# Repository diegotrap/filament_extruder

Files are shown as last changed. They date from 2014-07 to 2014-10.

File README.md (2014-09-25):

Filament Extruder
=================

Filament Extruder is a project dedicated to develop a simple, economic and easy to build filament extruding machine. It starts as an academic project at University Carlos III of Madrid.

Currently, the project is being prototyped and documented. The features of the present prototype are:

* Variable speed drive.
* Three independent temperature zones.
* Modular design, subsystems are mounted on an aluminium rail.
* Arduino controlled.
* LCD and encoder user interface.
* Variable speed pulling system.
* Fan cooling system.

Extruded product results have been documented to be:

* Filament usable for 3D printing.
* Up to 0.4 kg/h throughput.
* Up to +- 0.49 mm tolerance (quite bad result by now).

A video of the machine working can be found at http://youtu.be/RHb1_fSeXK4.

Images of the extrusion system:

*Extrusion line:*

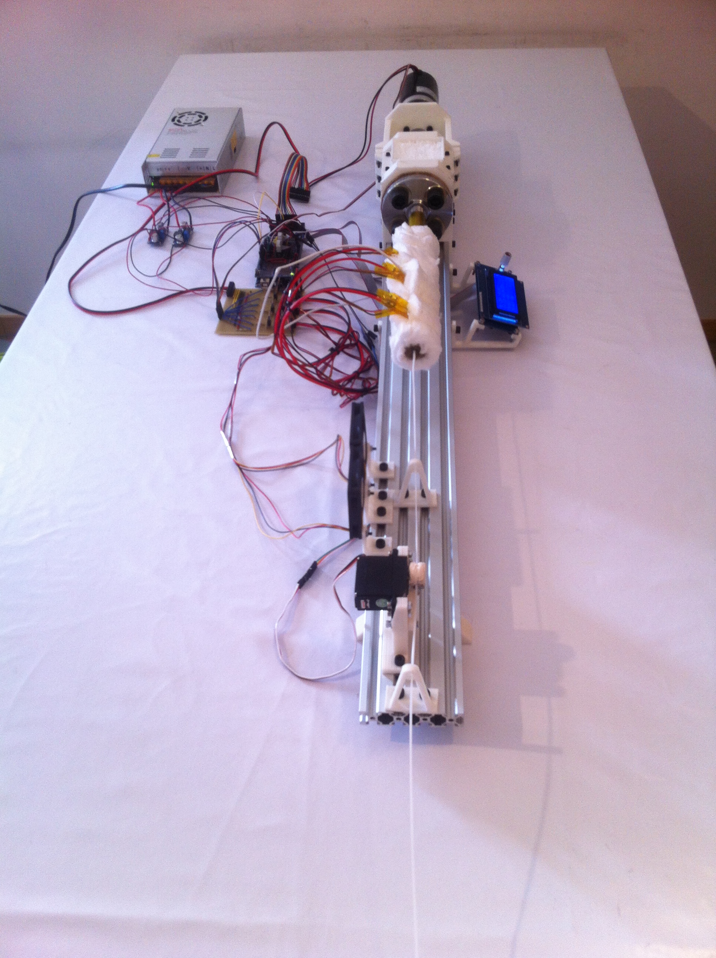
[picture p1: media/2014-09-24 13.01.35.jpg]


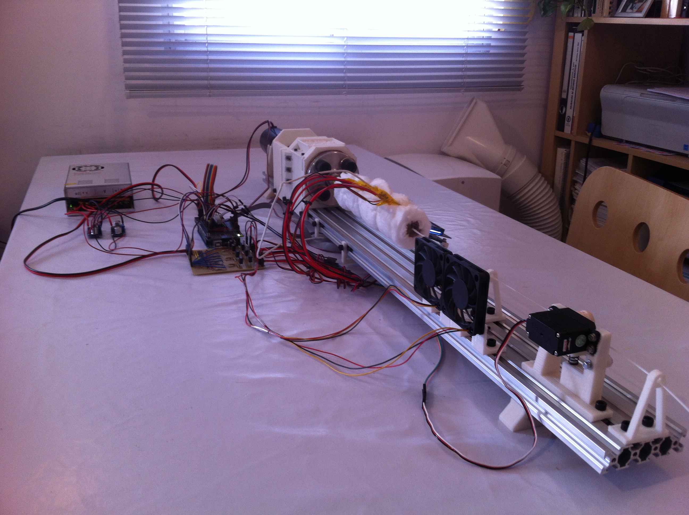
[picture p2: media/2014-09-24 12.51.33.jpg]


*Puller and cooling fans:*

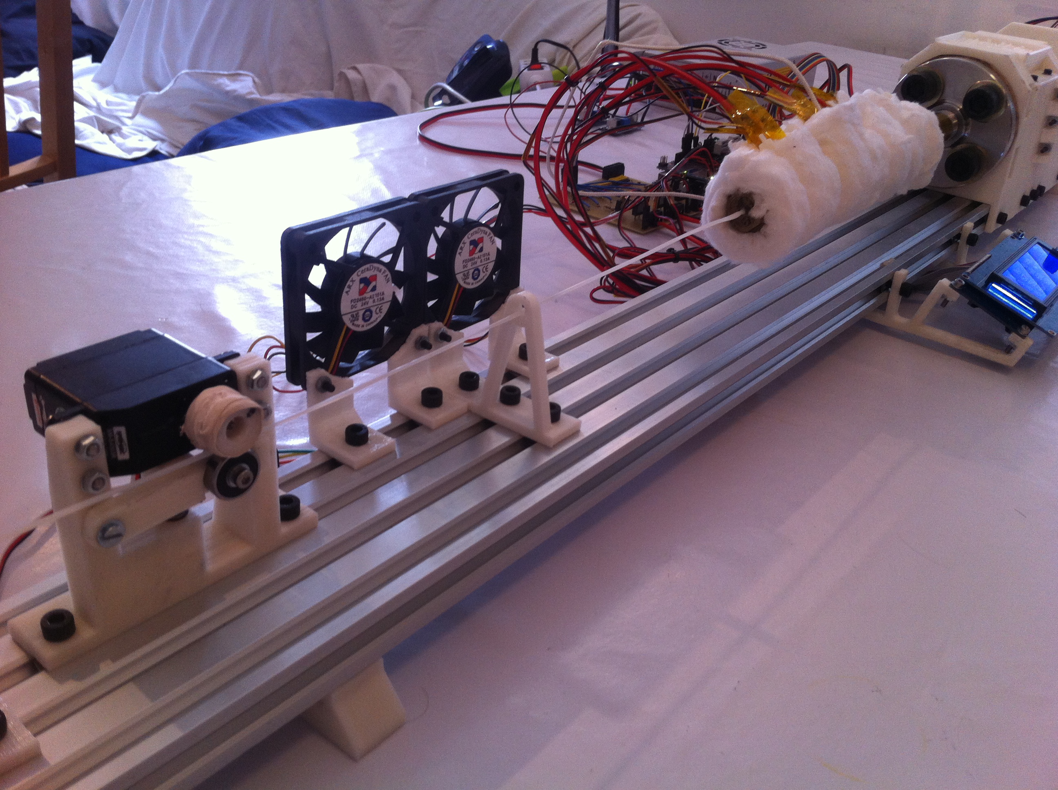
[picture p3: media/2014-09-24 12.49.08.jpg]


*Extruder and electronics:*

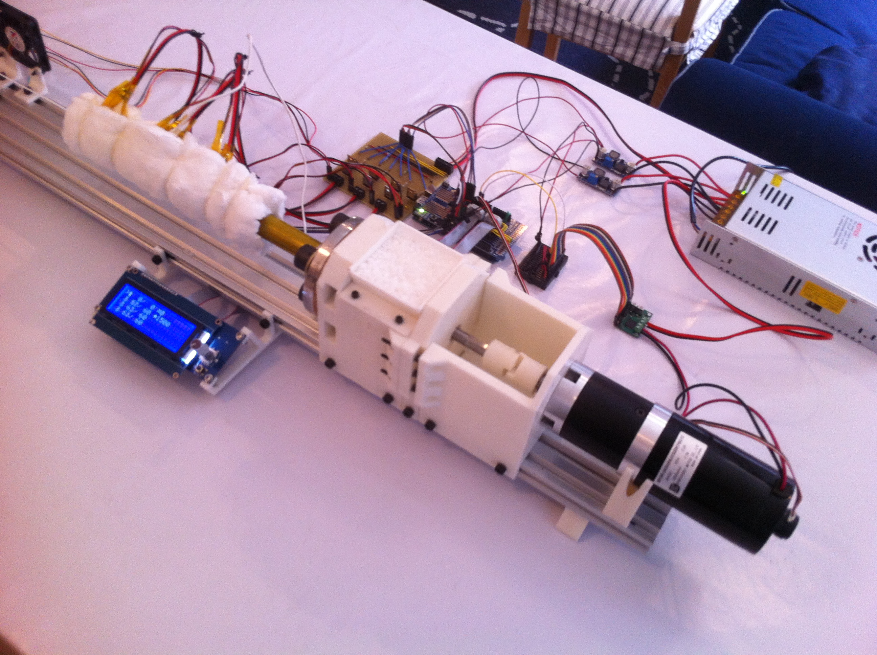
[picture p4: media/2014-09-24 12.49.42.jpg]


*Extruder body:*

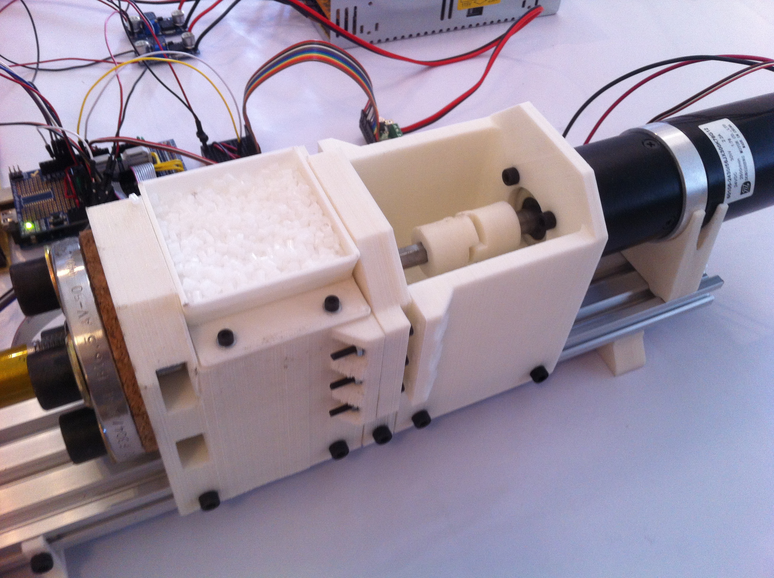
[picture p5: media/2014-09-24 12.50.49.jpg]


*Electronics:*

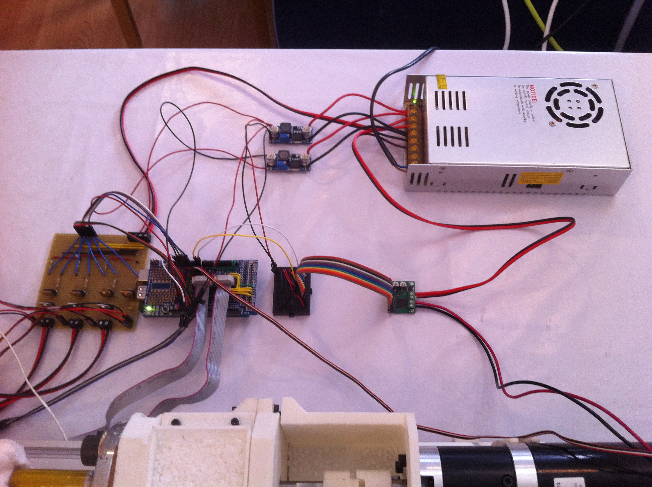
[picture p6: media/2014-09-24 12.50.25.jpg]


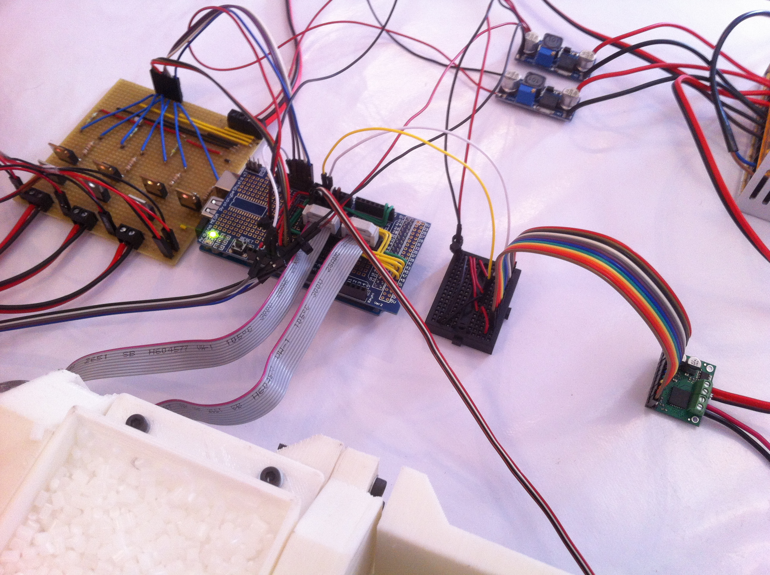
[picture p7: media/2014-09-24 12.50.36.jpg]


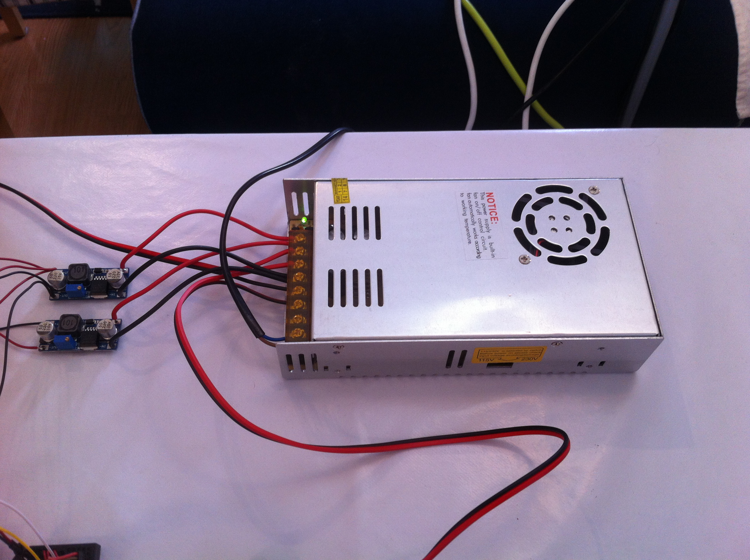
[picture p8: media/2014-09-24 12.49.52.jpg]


*LCD+encoder interface:*

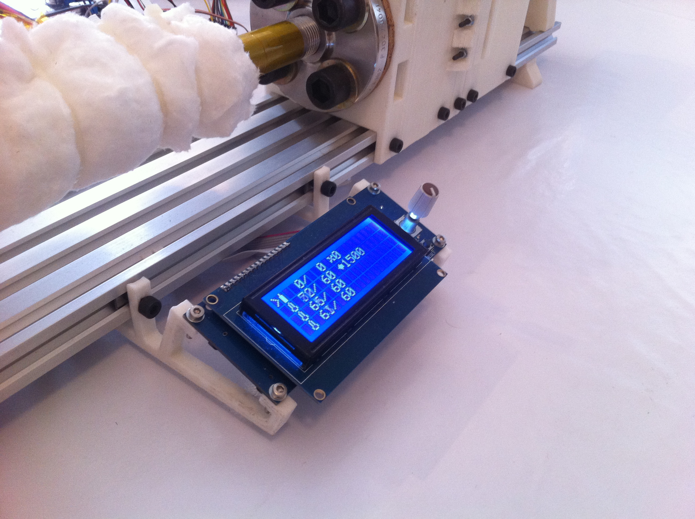
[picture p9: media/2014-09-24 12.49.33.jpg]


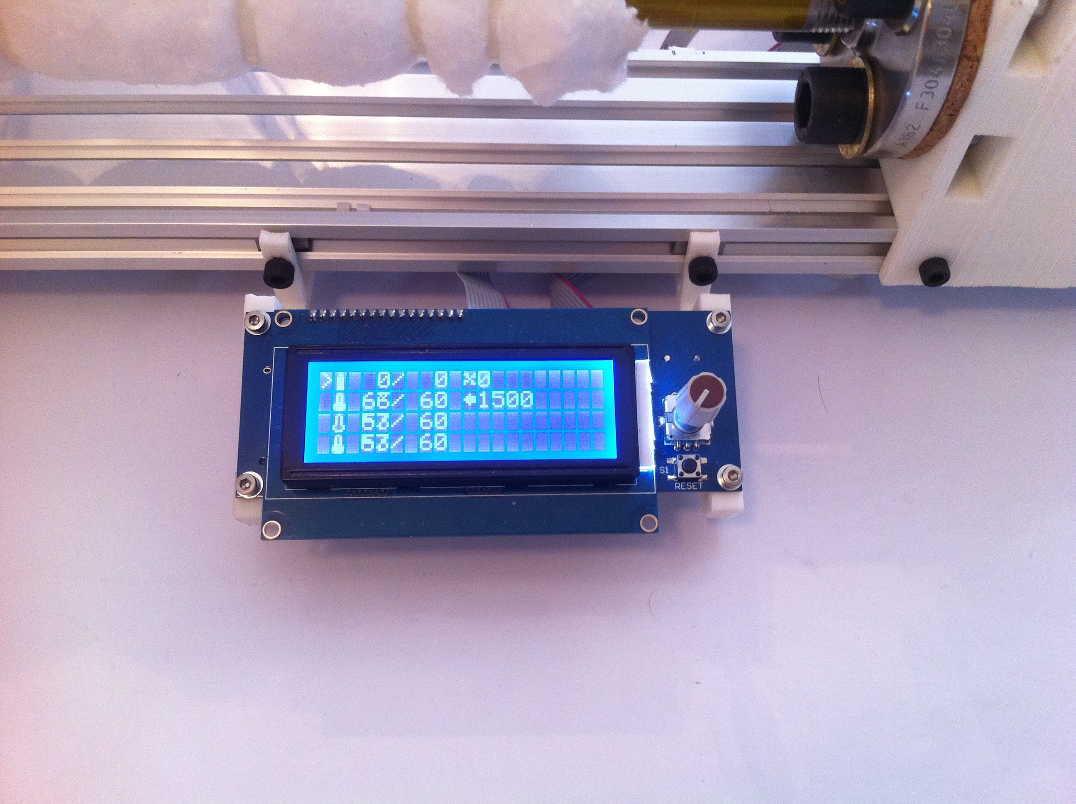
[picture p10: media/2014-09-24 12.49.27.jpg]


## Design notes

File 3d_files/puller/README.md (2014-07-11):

# Puller

**Note:** This is a first prototype of the puller and a work in progress. 

The **puller** is a subsystem of the filament extruder line that hauls off the solidified filament coming out of the extruder at a controlled speed.

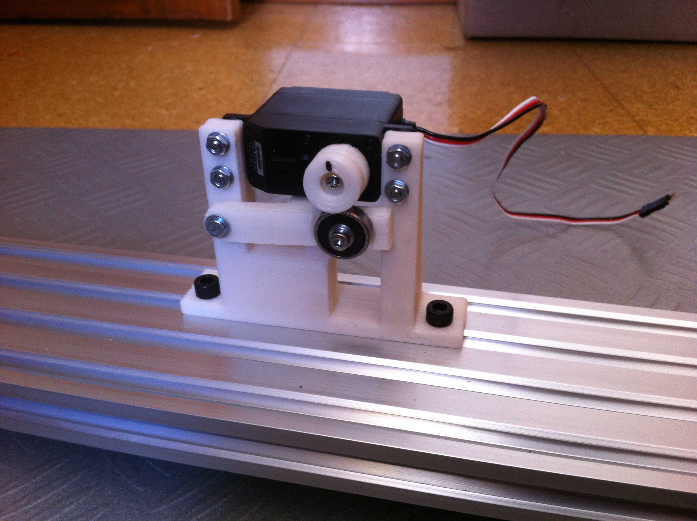
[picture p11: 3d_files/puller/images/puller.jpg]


## Parts

The parts necessary for building one puller (first prototype) are:

* 1 `puller_structure_simplified_fixed` (printed part)
* 1 `puller_lever_with_spring` (printed part)
* 1 `puller_wheel` (printed part)
* 1 continuous rotation servo (I use this one: http://www.pololu.com/product/1248)
* 1 625-2RS radial ball bearing
* 1 spring
* 5 M3x16 screws
* 1 M3x20 screw
* 5 M3 nuts
* 1 M3 self-locking nut
* 13 M3 washers
* Optional: 2 M5x10 screws and 2 t-nuts are necessary for fixing the puller to a v-slot profile.

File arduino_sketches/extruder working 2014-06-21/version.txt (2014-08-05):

versión que tiene el menú de pantalla y algunas funciones como RGB Led, etc, pero presenta bugs en la interfaz

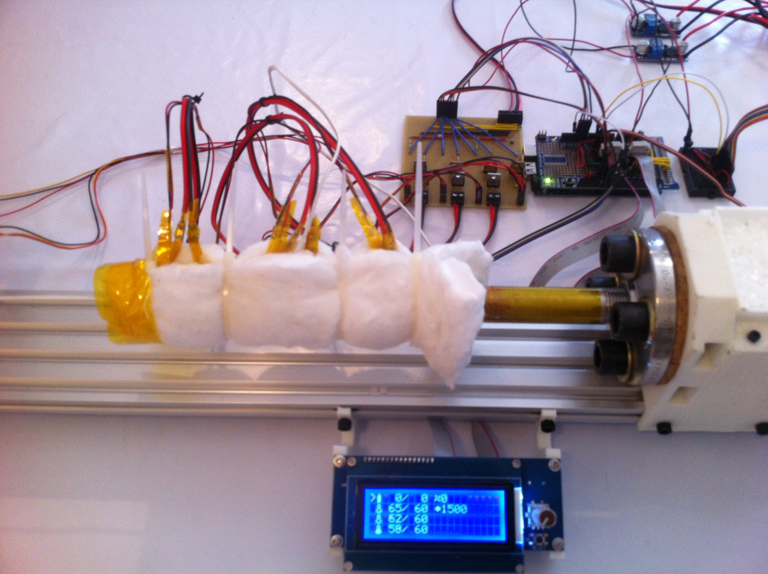
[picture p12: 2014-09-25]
media/2014-09-24 12.47.06.jpg

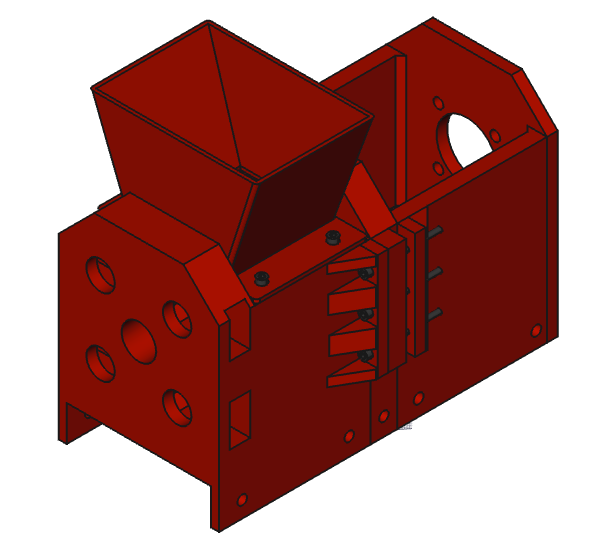
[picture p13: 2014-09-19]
media/FreeCAD_4.png

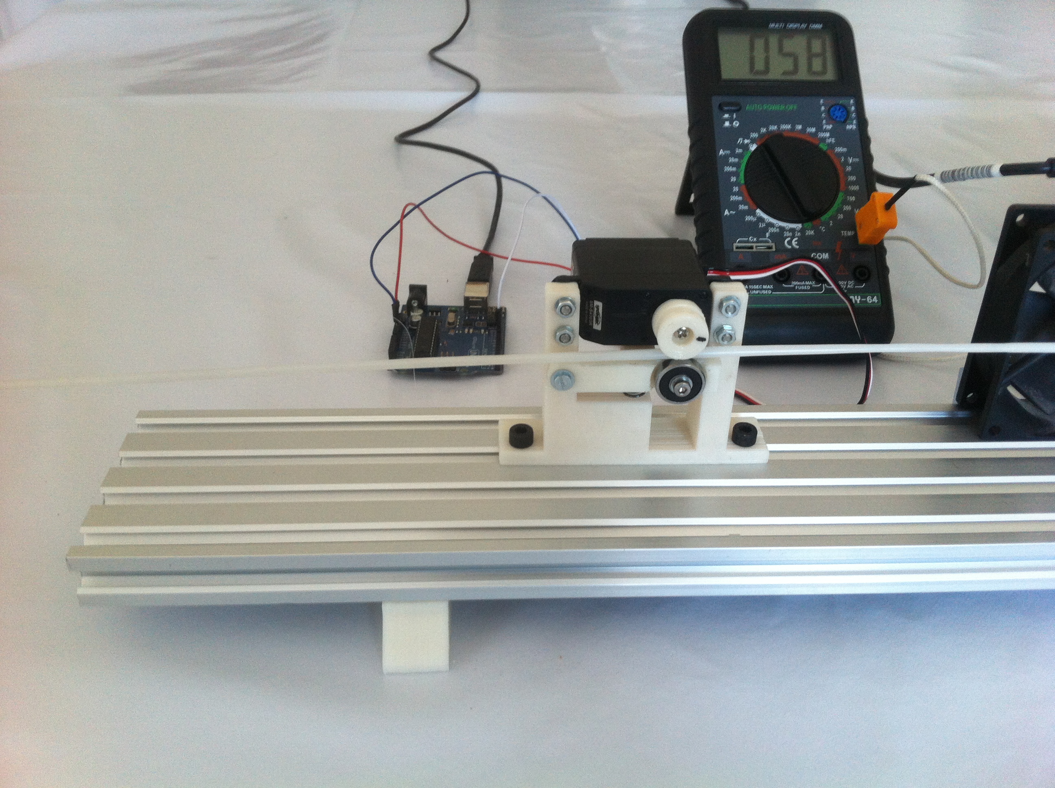
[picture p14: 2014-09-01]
media/2014-08-16 19.02.47.jpg

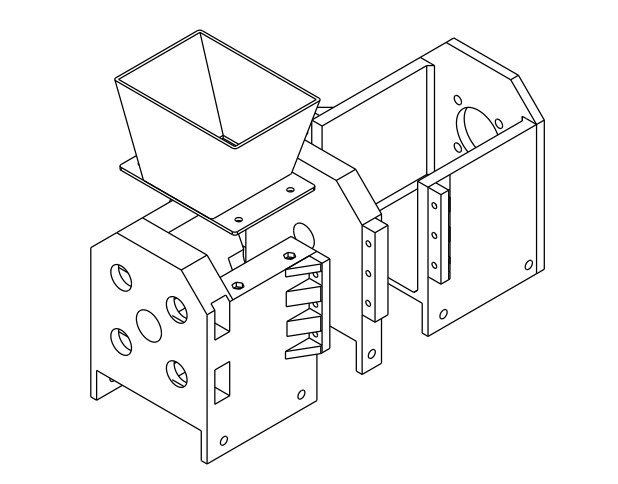
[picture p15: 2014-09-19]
media/unibody_drive_exploded_view_pdf__1_page_.png

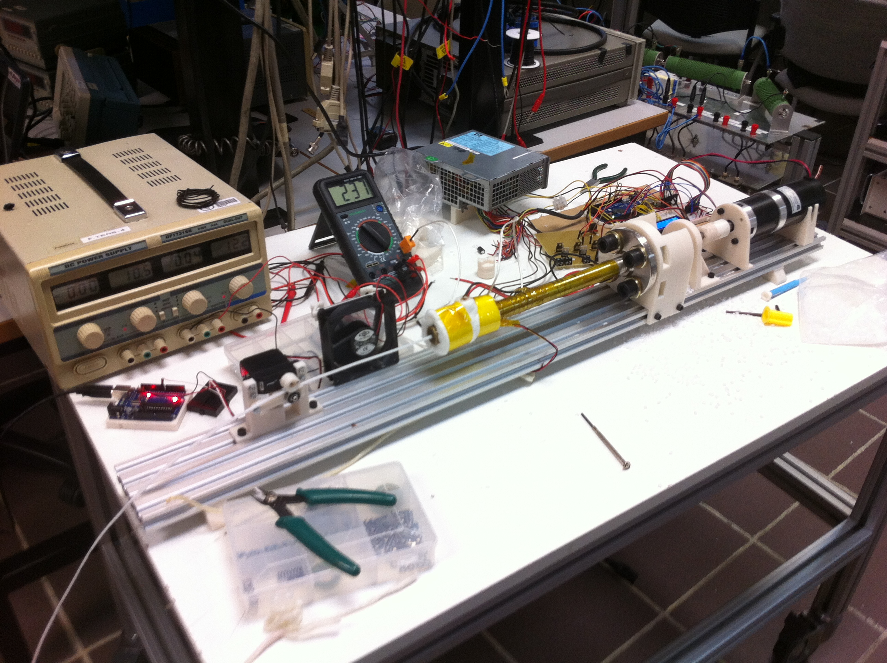
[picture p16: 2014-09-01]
media/2014-07-29 19.45.26.jpg

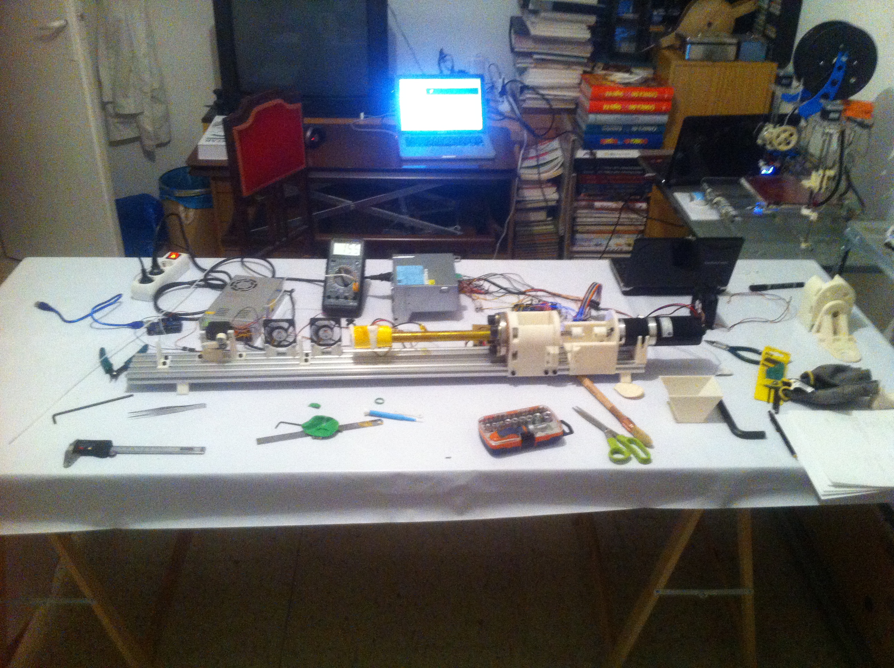
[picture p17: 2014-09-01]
media/2014-08-18 22.53.50.jpg

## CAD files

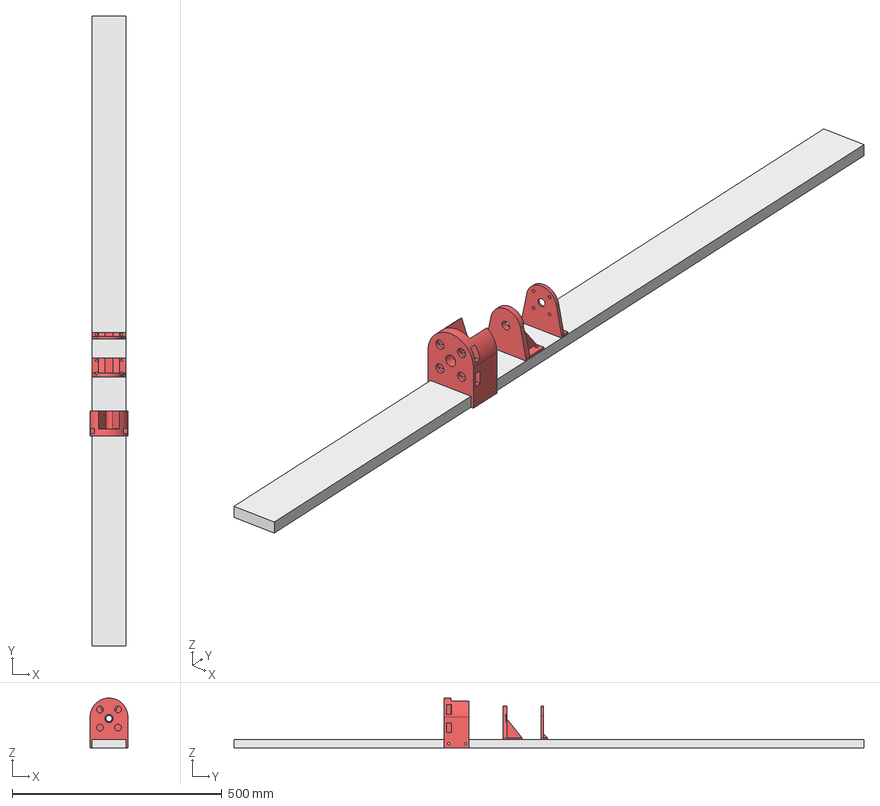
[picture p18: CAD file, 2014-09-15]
3d_files/drive/first_prototype/prototype_assembly.fcstd
90.0 x 1500.0 x 118.8 mm
hopper_and_barrel_support
thrust_bearing_support
motor_support
vslot

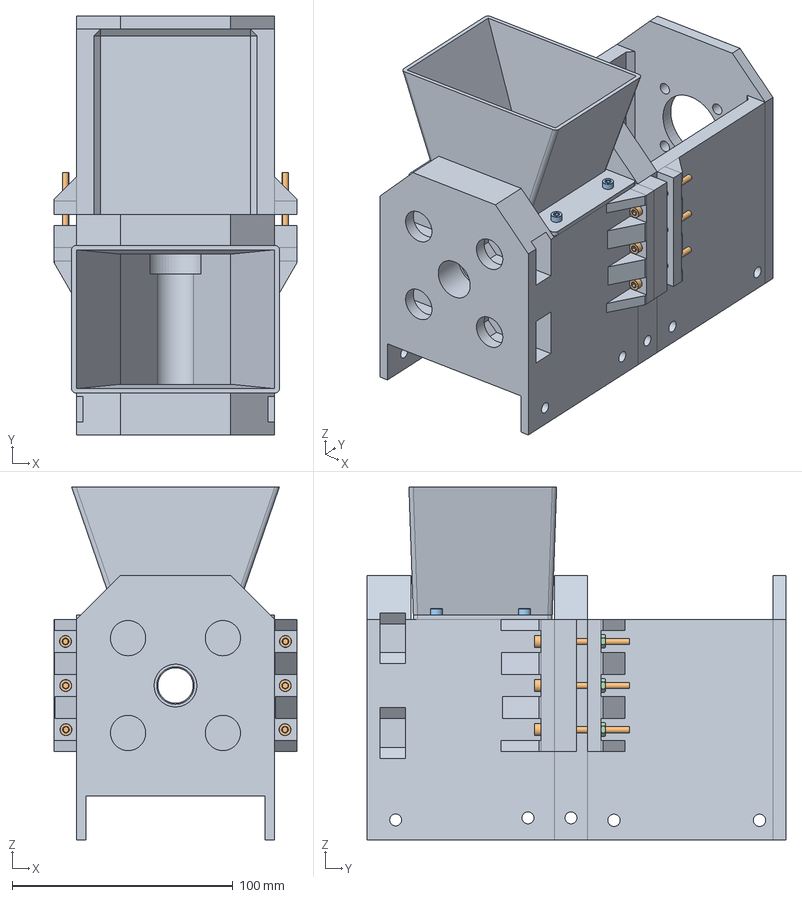
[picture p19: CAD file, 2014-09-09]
3d_files/drive/unibody_drive_i2/assembly/unibody_drive_assembled.fcstd
110.0 x 190.0 x 160.0 mm
printed_parts
M3x40_screws
M3_hopper_screws
M3_nuts

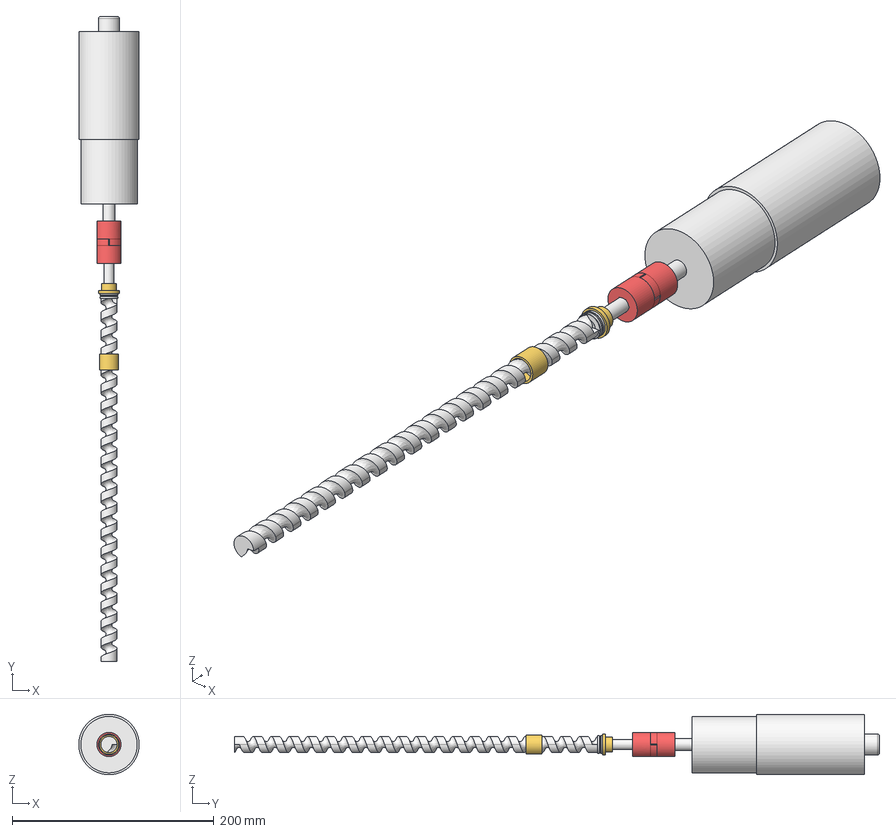
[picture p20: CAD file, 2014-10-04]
3d_files/extruder_assembly/mechanical_assembly.fcstd
59.9 x 640.0 x 60.0 mm
flanged_bearing
plain_bearing
thrust_bearing
motor
shaft_coupler_hex
shaft_coupler_keyway
screw

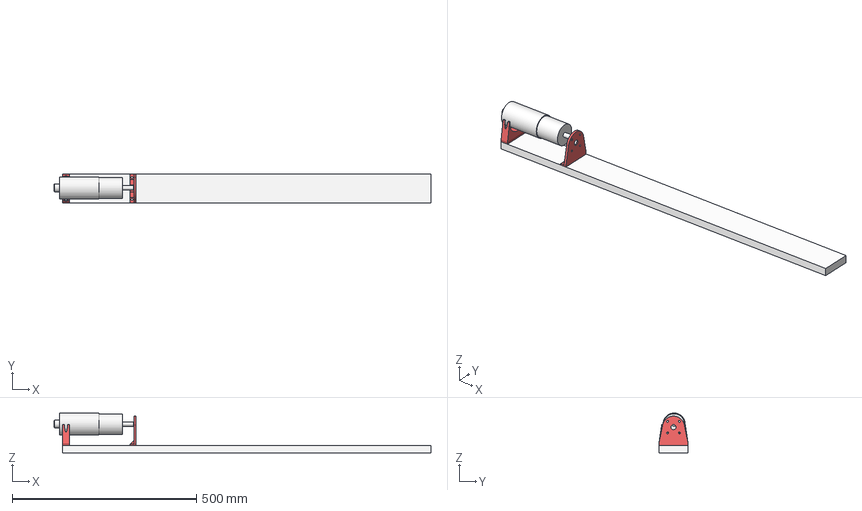
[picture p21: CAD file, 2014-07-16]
3d_files/filament_line_assembly.fcstd
1022.5 x 80.0 x 108.4 mm
vslot
motor_torsion_support
vslot_motor_support_big
motor_simplified

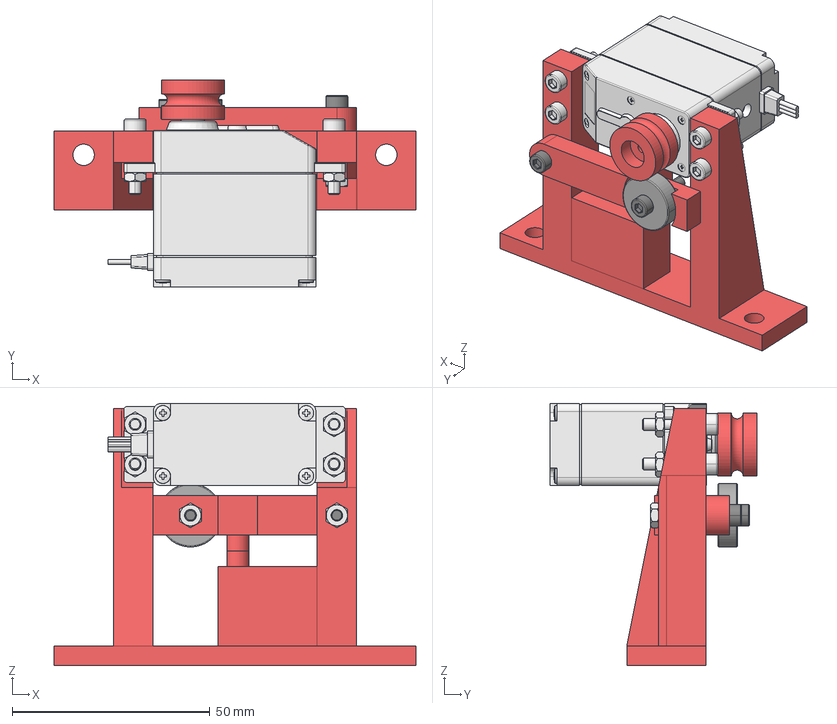
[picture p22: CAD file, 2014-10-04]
3d_files/extruder_assembly/puller_assembly.fcstd
91.5 x 52.3 x 66.3 mm
puller_structure
puller_lever
M3x20_001
625-2RS_ball_bearing
M3x16_001
M3_nut_001
M3_nut_002
Servo-SM-S4303R
servo_nuts_and_bolts
puller_wheel

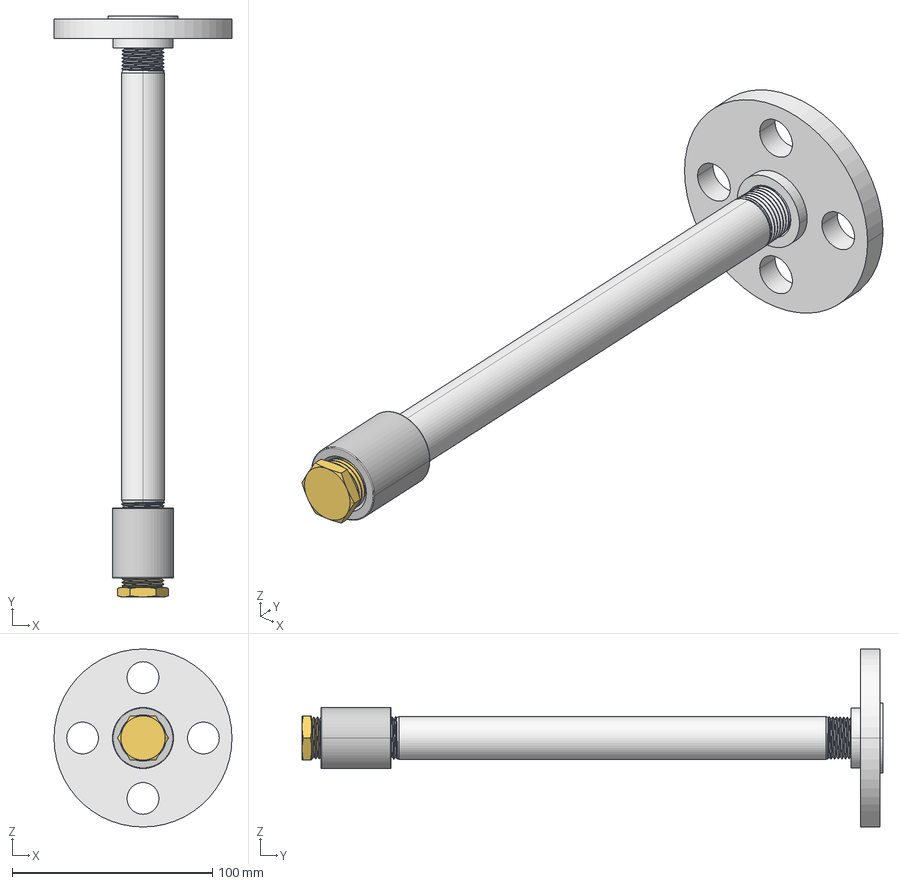
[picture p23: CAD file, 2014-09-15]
3d_files/barrel/barrel_assembly.fcstd
88.9 x 290.1 x 88.9 mm
4452K114
4452K144
4548K181
44695K11

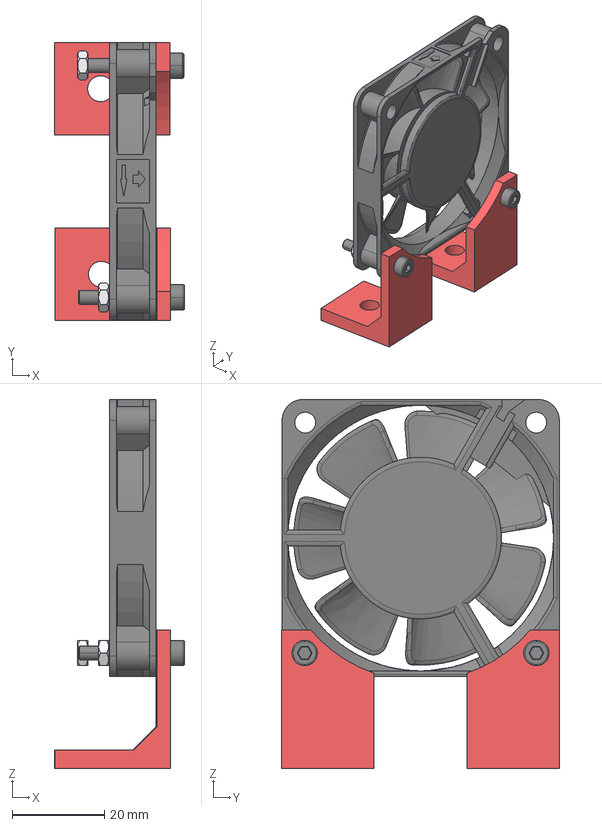
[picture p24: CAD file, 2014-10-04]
3d_files/extruder_assembly/fan_assembly.fcstd
28.2 x 60.1 x 79.9 mm
DC_fan_60x60x10
fan_holder_right
M3x20_004
M3x20_003
M3_nut_007
M3_nut_008
fan_holder_left

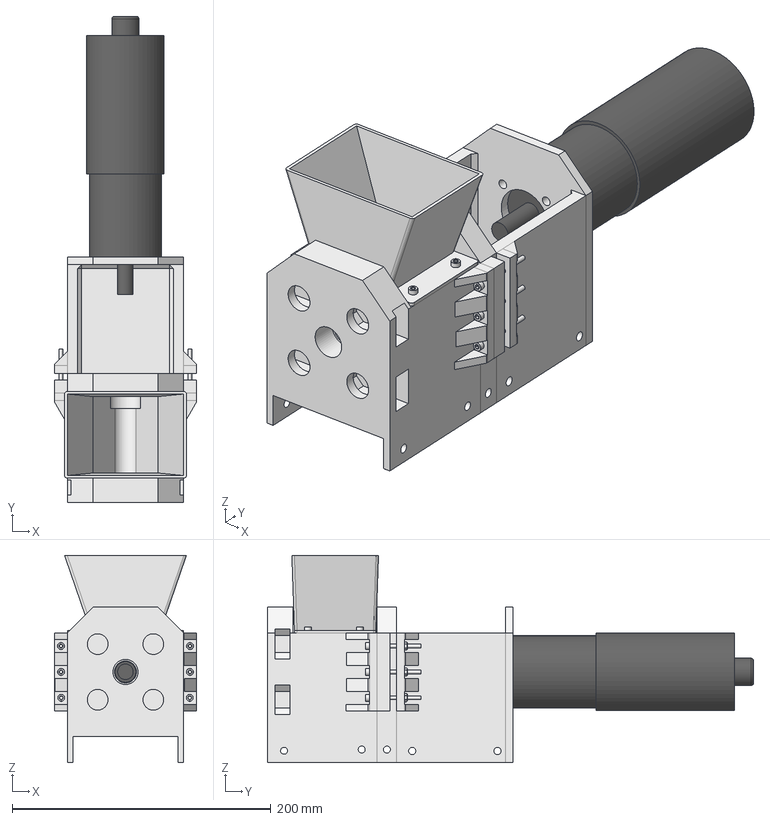
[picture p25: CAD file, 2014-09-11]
3d_files/extruder_assembly/unibody_drive_assembled.fcstd
110.0 x 376.0 x 160.0 mm
printed_parts
M3x40_screws
M3_hopper_screws
M3_nuts
motor

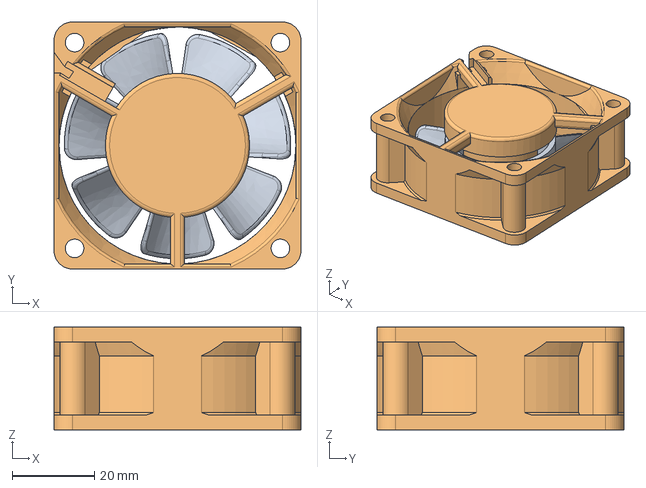
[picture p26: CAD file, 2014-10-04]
3d_files/cooling/Fan 60x60x25mm.stp
60.0 x 60.0 x 25.0 mm

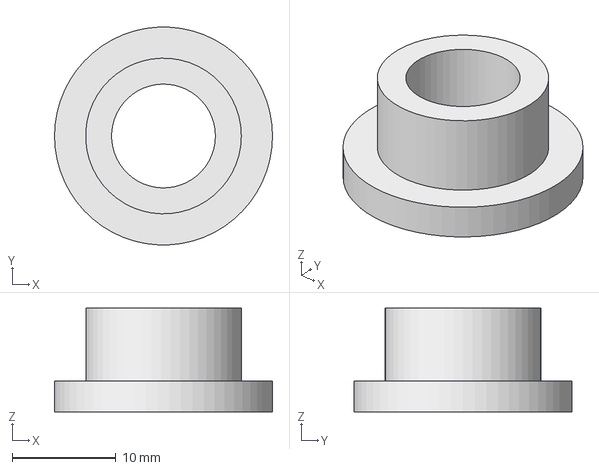
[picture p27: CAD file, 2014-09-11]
3d_files/drive/bearings/flanged_bearing.fcstd
21.0 x 21.0 x 10.0 mm

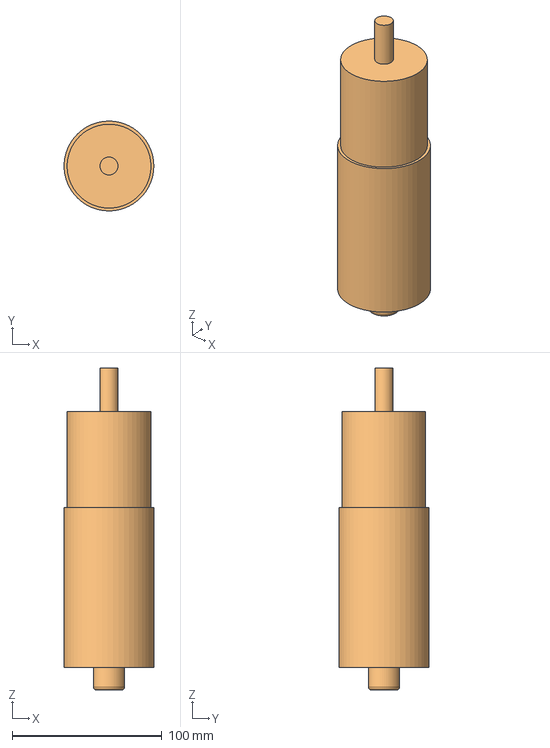
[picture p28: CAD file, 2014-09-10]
3d_files/drive/motor/motor_simplified.fcstd
59.9 x 60.0 x 215.0 mm

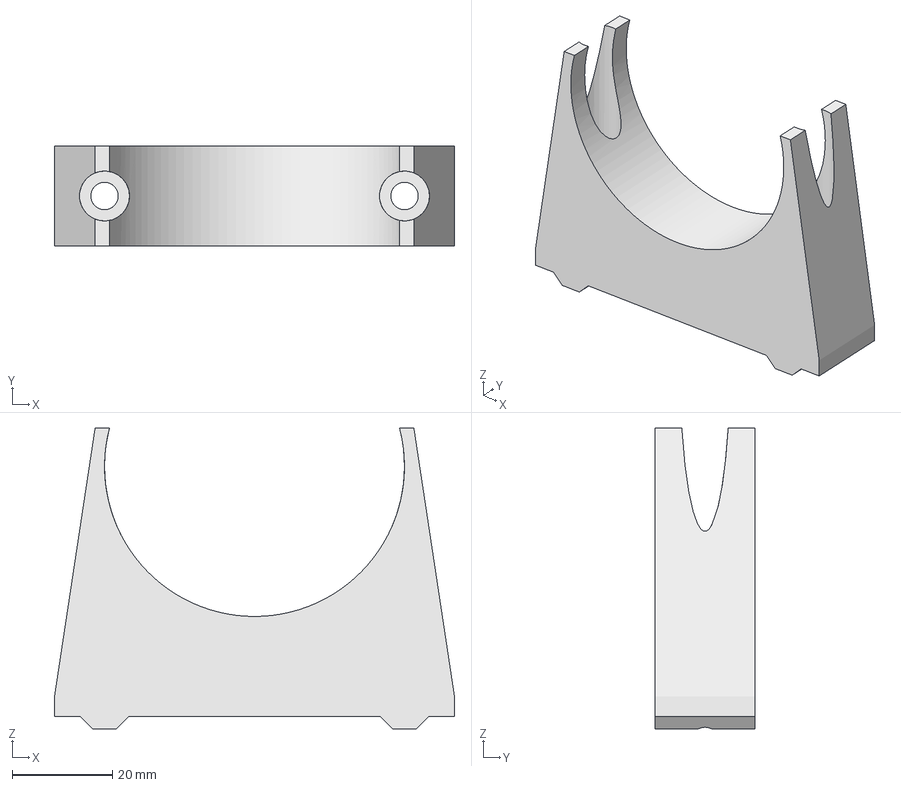
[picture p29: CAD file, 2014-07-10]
3d_files/drive/motor_weight_supports/vslot_motor_support_big.fcstd
80.0 x 20.0 x 60.2 mm

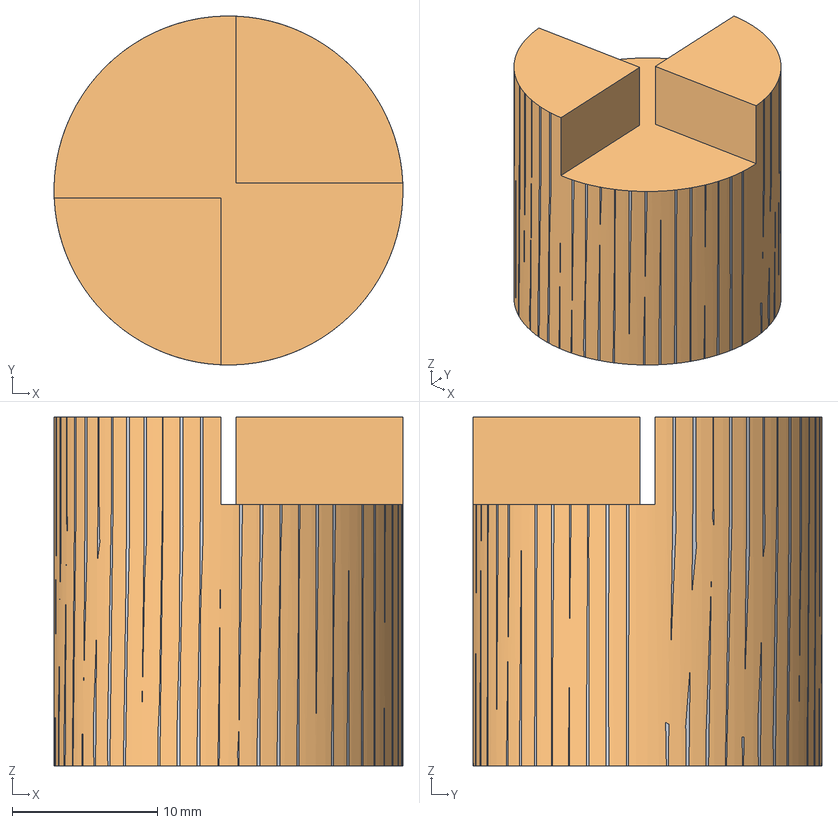
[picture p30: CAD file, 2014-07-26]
3d_files/drive/shaft_couplers/shaft_coupler_hex.fcstd
24.0 x 24.0 x 24.0 mm
Pocket (Meshed)

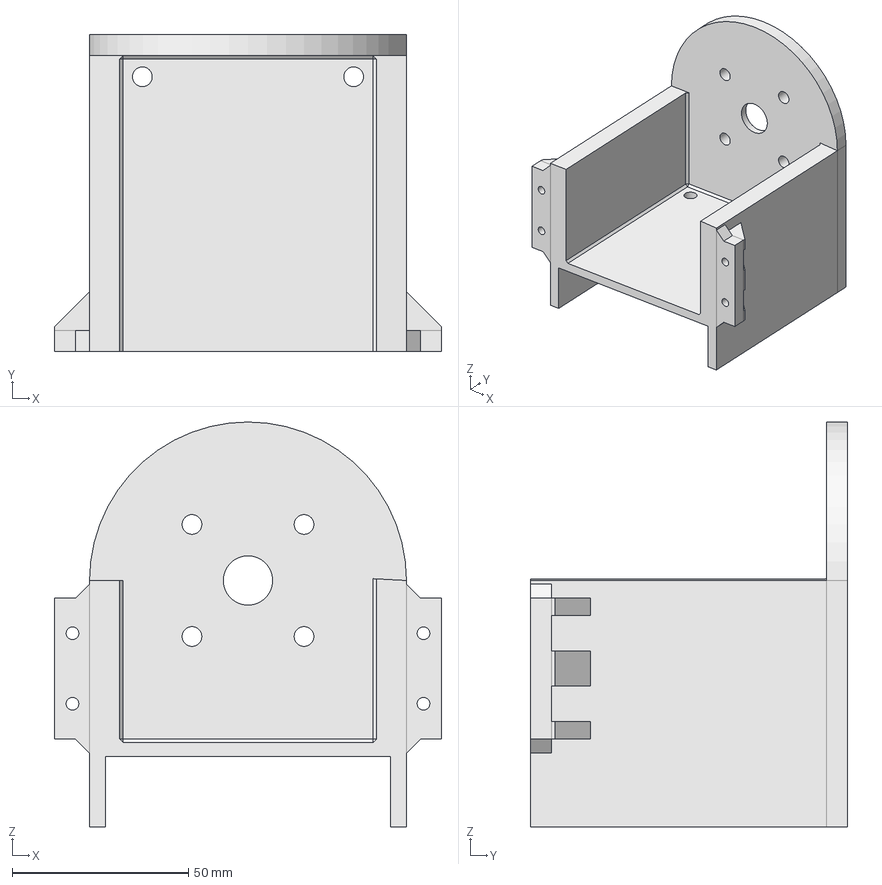
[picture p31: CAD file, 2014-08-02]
3d_files/drive/unibody_drive/motor_support.fcstd
110.0 x 90.0 x 115.0 mm

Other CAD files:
3d_files/drive/unibody_drive_i2/parts/thrust_bearing_support.fcstd
3d_files/other/lcd_holder.fcstd
3d_files/puller/bearing_625_0.stp
3d_files/spool/spool.FCStd
3d_files/barrel/4452K114.STEP
3d_files/barrel/4452K144.STEP
3d_files/barrel/44695K110.STEP
3d_files/barrel/4548K181.STEP
3d_files/cooling/DC_fan_60x60x10.FCStd
3d_files/cooling/fan_duct.fcstd
3d_files/cooling/fan_holder_left.fcstd
3d_files/cooling/fan_holder_left.stl
3d_files/cooling/fan_holder_right.fcstd
3d_files/cooling/fan_holder_right.stl
3d_files/cooling/fan_support.fcstd
3d_files/cooling/vslot_fan_foot.fcstd
3d_files/drive/bearings/plain_bearing.FCStd
3d_files/drive/bearings/thrust_bearing.fcstd
3d_files/drive/first_prototype/motor_torsion_support.fcstd
3d_files/drive/first_prototype/motor_torsion_support.stl
3d_files/drive/first_prototype/pipe_and_hopper_strong.fcstd
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

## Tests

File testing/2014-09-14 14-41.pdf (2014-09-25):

## Datos de la muestra

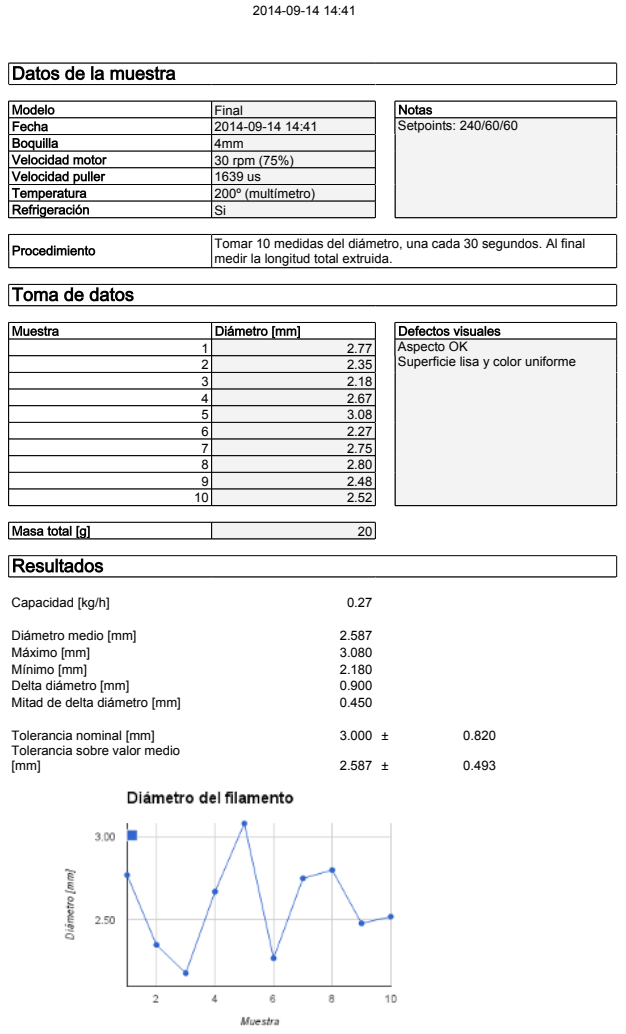
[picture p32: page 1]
Modelo; Final; Notas; Fecha; Setpoints: 240/60/60; Procedimiento; Tomar 10 medidas del diámetro, una cada 30 segundos. Al final; Muestra; Diámetro [mm]; Defectos visuales; Aspecto OK; Superficie lisa y color uniforme; Masa total [g]; Resultados; Capacidad [kg/h]; Diámetro medio [mm]; Máximo [mm]; Mínimo [mm]; Delta diámetro [mm]; Mitad de delta diámetro [mm]; Tolerancia nominal [mm]

Boquilla | 4mm
Velocidad motor | 30 rpm (75%)
Velocidad puller | 1639 us
Temperatura | 200º (multímetro)
Refrigeración | Si

medir la longitud total extruida.

Toma de datos

3 | 2.18
4 | 2.67
5 | 3.08
6 | 2.27
7 | 2.75
8 | 2.80
9 | 2.48
10 | 2.52

Tolerancia sobre valor medio

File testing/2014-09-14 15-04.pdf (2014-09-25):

## Datos de la muestra

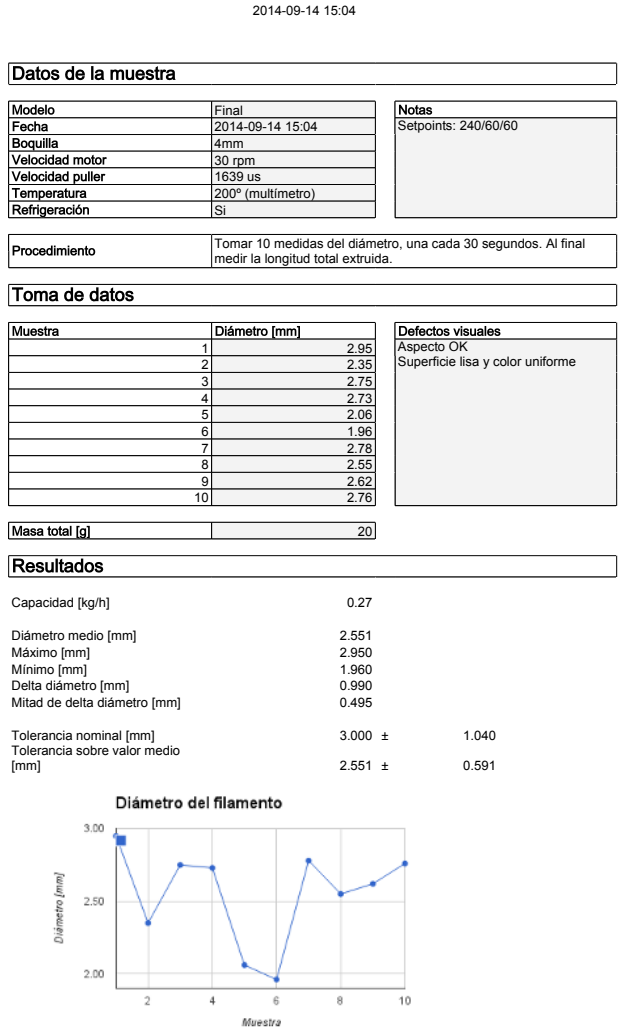
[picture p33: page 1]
Modelo; Final; Notas; Fecha; Setpoints: 240/60/60; Procedimiento; Tomar 10 medidas del diámetro, una cada 30 segundos. Al final; Muestra; Diámetro [mm]; Defectos visuales; Aspecto OK; Superficie lisa y color uniforme; Masa total [g]; Resultados; Capacidad [kg/h]; Diámetro medio [mm]; Máximo [mm]; Mínimo [mm]; Delta diámetro [mm]; Mitad de delta diámetro [mm]; Tolerancia nominal [mm]

Boquilla | 4mm
Velocidad motor | 30 rpm
Velocidad puller | 1639 us
Temperatura | 200º (multímetro)
Refrigeración | Si

medir la longitud total extruida.

Toma de datos

3 | 2.75
4 | 2.73
5 | 2.06
6 | 1.96
7 | 2.78
8 | 2.55
9 | 2.62
10 | 2.76

Tolerancia sobre valor medio

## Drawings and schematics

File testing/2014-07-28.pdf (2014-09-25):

## Datos de la muestra

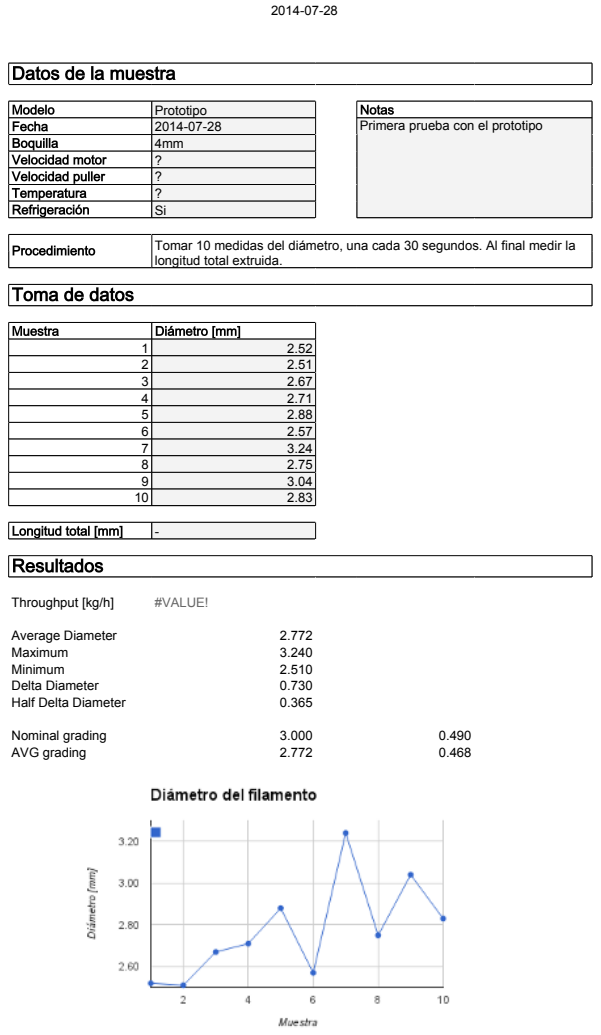
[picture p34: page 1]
Modelo; Prototipo; Notas; Fecha; Primera prueba con el prototipo; Procedimiento; Tomar 10 medidas del diámetro, una cada 30 segundos. Al final medir la; Longitud total [mm]; Resultados; Throughput [kg/h]; #VALUE!; Average Diameter; Maximum; Minimum; Delta Diameter; Half Delta Diameter; Nominal grading; AVG grading

Boquilla | 4mm
Velocidad motor | ?
Velocidad puller | ?
Temperatura | ?
Refrigeración | Si

longitud total extruida.

Toma de datos

Muestra | Diámetro [mm]

1 | 2.52
2 | 2.51
3 | 2.67
4 | 2.71
5 | 2.88
6 | 2.57
7 | 3.24
8 | 2.75
9 | 3.04
10 | 2.83

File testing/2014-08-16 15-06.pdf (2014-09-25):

## Datos de la muestra

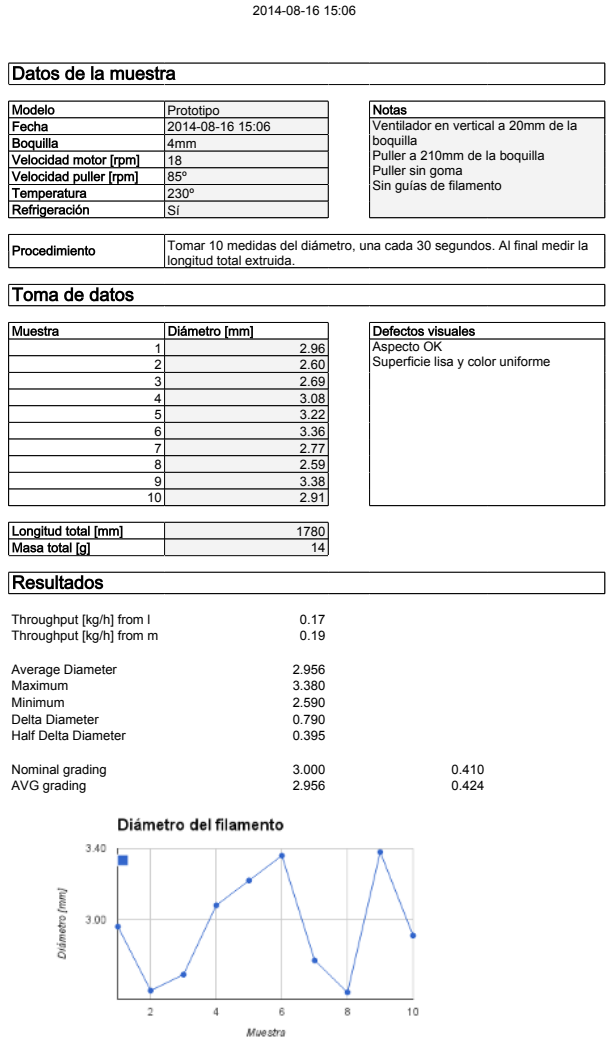
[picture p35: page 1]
Modelo; Prototipo; Notas; Fecha; Ventilador en vertical a 20mm de la; Procedimiento; Tomar 10 medidas del diámetro, una cada 30 segundos. Al final medir la; Muestra; Diámetro [mm]; Defectos visuales; Aspecto OK; Superficie lisa y color uniforme; Resultados; Throughput [kg/h] from l; Throughput [kg/h] from m; Average Diameter; Maximum; Minimum; Delta Diameter; Half Delta Diameter; Nominal grading; AVG grading

Boquilla | 4mm
Velocidad motor [rpm] | 18
Velocidad puller [rpm] | 85º
Temperatura | 230º
Refrigeración | Sí

boquilla
Puller a 210mm de la boquilla
Puller sin goma
Sin guías de filamento

longitud total extruida.

Toma de datos

3 | 2.69
4 | 3.08
5 | 3.22
6 | 3.36
7 | 2.77
8 | 2.59
9 | 3.38
10 | 2.91

Longitud total [mm] | 1780
Masa total [g] | 14

2014-08-16 15:06

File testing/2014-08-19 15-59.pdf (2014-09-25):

## Datos de la muestra

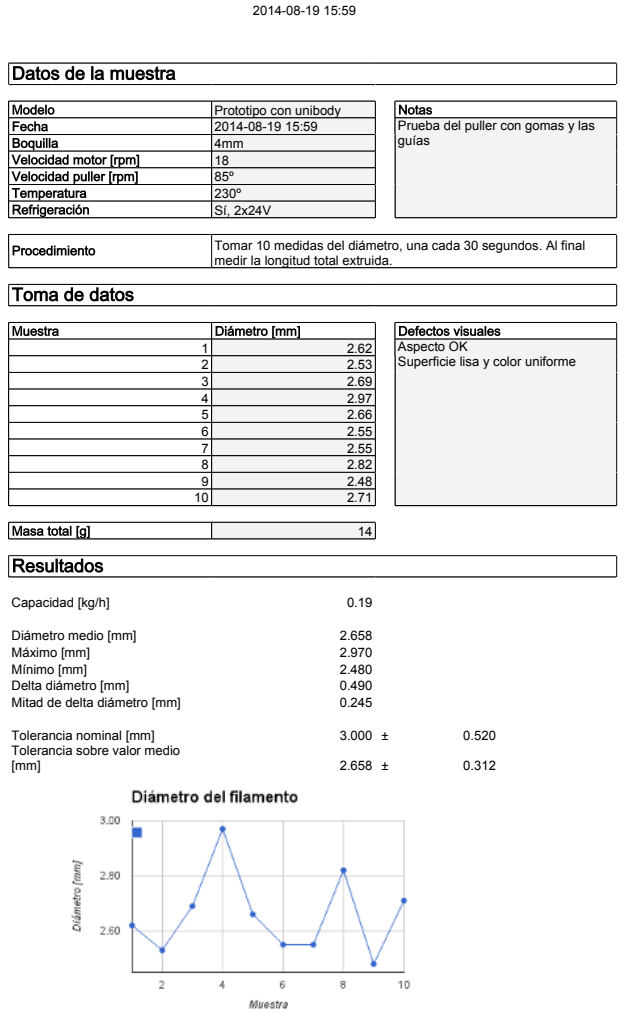
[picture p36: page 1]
Modelo; Prototipo con unibody; Notas; Fecha; Prueba del puller con gomas y las; Boquilla; guías; Procedimiento; Tomar 10 medidas del diámetro, una cada 30 segundos. Al final; Muestra; Diámetro [mm]; Defectos visuales; Aspecto OK; Superficie lisa y color uniforme; Masa total [g]; Resultados; Capacidad [kg/h]; Diámetro medio [mm]; Máximo [mm]; Mínimo [mm]; Delta diámetro [mm]; Mitad de delta diámetro [mm]; Tolerancia nominal [mm]

Velocidad motor [rpm] | 18
Velocidad puller [rpm] | 85º
Temperatura | 230º
Refrigeración | Sí, 2x24V

medir la longitud total extruida.

Toma de datos

3 | 2.69
4 | 2.97
5 | 2.66
6 | 2.55
7 | 2.55
8 | 2.82
9 | 2.48
10 | 2.71

Tolerancia sobre valor medio

2014-08-19 15:59

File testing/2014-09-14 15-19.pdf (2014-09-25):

## Datos de la muestra

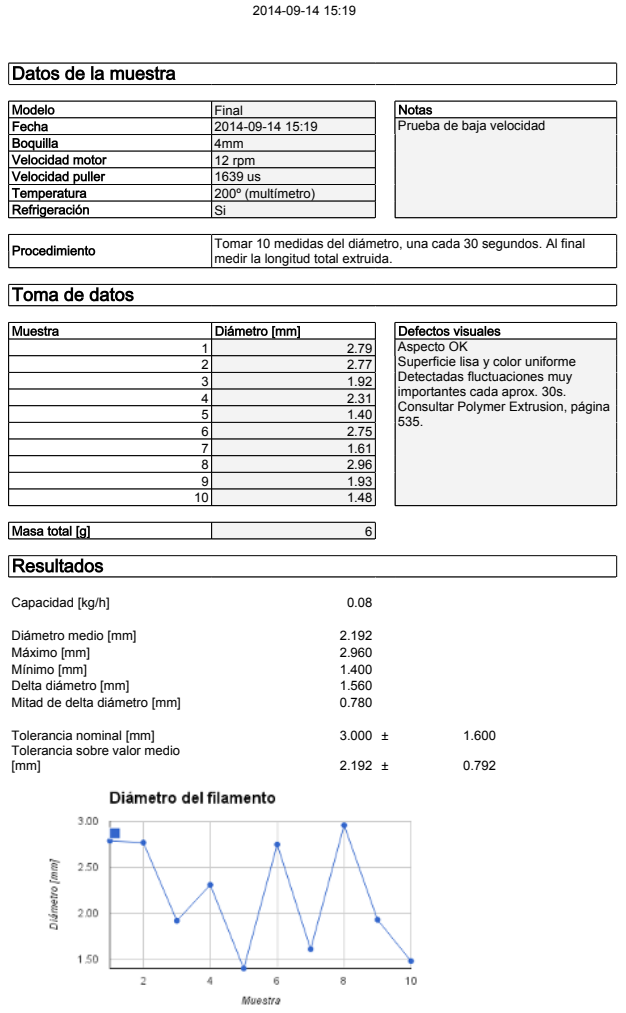
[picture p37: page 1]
Modelo; Final; Notas; Fecha; Prueba de baja velocidad; Procedimiento; Tomar 10 medidas del diámetro, una cada 30 segundos. Al final; Muestra; Diámetro [mm]; Defectos visuales; Aspecto OK; Masa total [g]; Resultados; Capacidad [kg/h]; Diámetro medio [mm]; Máximo [mm]; Mínimo [mm]; Delta diámetro [mm]; Mitad de delta diámetro [mm]; Tolerancia nominal [mm]

Boquilla | 4mm
Velocidad motor | 12 rpm
Velocidad puller | 1639 us
Temperatura | 200º (multímetro)
Refrigeración | Si

medir la longitud total extruida.

Toma de datos

2 | 2.77
3 | 1.92
4 | 2.31
5 | 1.40
6 | 2.75
7 | 1.61
8 | 2.96
9 | 1.93
10 | 1.48

Superficie lisa y color uniforme
Detectadas fluctuaciones muy
importantes cada aprox. 30s.
Consultar Polymer Extrusion, página

Tolerancia sobre valor medio

2014-09-14 15:19

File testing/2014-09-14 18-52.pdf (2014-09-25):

## Datos de la muestra

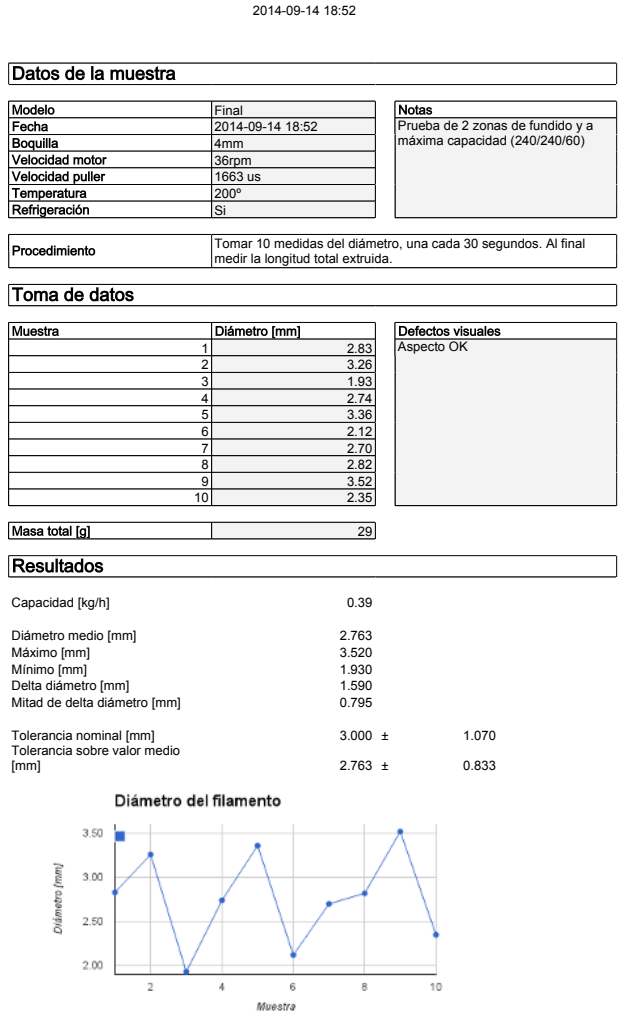
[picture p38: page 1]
Modelo; Final; Notas; Fecha; Prueba de 2 zonas de fundido y a; Boquilla; máxima capacidad (240/240/60); Procedimiento; Tomar 10 medidas del diámetro, una cada 30 segundos. Al final; Muestra; Diámetro [mm]; Defectos visuales; Aspecto OK; Masa total [g]; Resultados; Capacidad [kg/h]; Diámetro medio [mm]; Máximo [mm]; Mínimo [mm]; Delta diámetro [mm]; Mitad de delta diámetro [mm]; Tolerancia nominal [mm]

Velocidad motor | 36rpm
Velocidad puller | 1663 us
Temperatura | 200º
Refrigeración | Si

medir la longitud total extruida.

Toma de datos

2 | 3.26
3 | 1.93
4 | 2.74
5 | 3.36
6 | 2.12
7 | 2.70
8 | 2.82
9 | 3.52
10 | 2.35

Tolerancia sobre valor medio

2014-09-14 18:52

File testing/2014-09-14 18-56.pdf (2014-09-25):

## Datos de la muestra

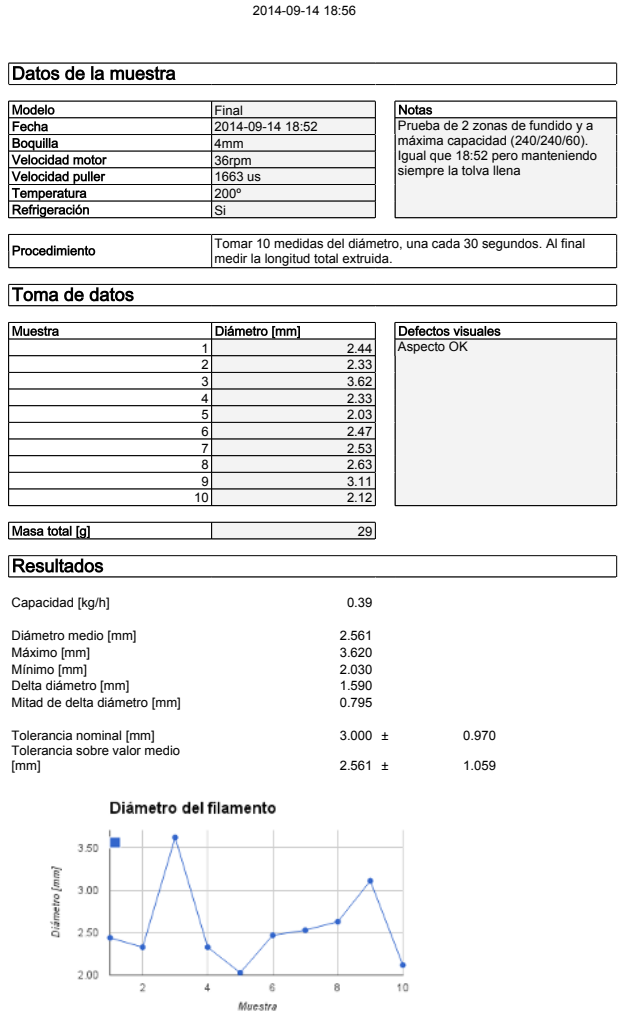
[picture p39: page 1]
Modelo; Final; Notas; Fecha; Prueba de 2 zonas de fundido y a; Procedimiento; Tomar 10 medidas del diámetro, una cada 30 segundos. Al final; Muestra; Diámetro [mm]; Defectos visuales; Aspecto OK; Masa total [g]; Resultados; Capacidad [kg/h]; Diámetro medio [mm]; Máximo [mm]; Mínimo [mm]; Delta diámetro [mm]; Mitad de delta diámetro [mm]; Tolerancia nominal [mm]

Boquilla | 4mm
Velocidad motor | 36rpm
Velocidad puller | 1663 us
Temperatura | 200º
Refrigeración | Si

máxima capacidad (240/240/60).
Igual que 18:52 pero manteniendo
siempre la tolva llena

medir la longitud total extruida.

Toma de datos

2 | 2.33
3 | 3.62
4 | 2.33
5 | 2.03
6 | 2.47
7 | 2.53
8 | 2.63
9 | 3.11
10 | 2.12

Tolerancia sobre valor medio

2014-09-14 18:56

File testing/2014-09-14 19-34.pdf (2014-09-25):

## Datos de la muestra

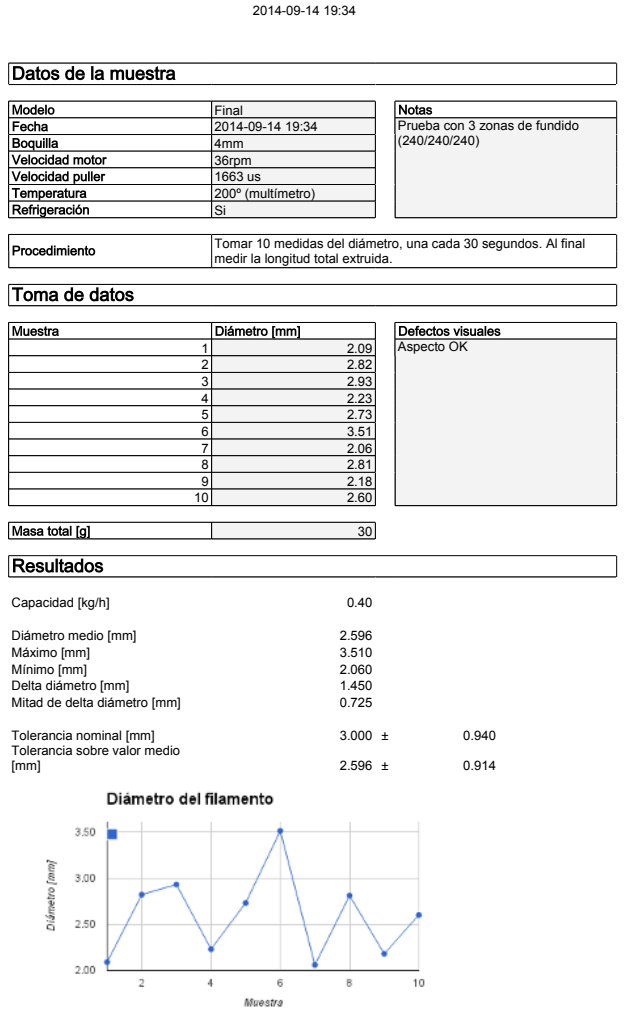
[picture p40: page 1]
Modelo; Final; Notas; Fecha; Prueba con 3 zonas de fundido; Boquilla; Procedimiento; Tomar 10 medidas del diámetro, una cada 30 segundos. Al final; Muestra; Diámetro [mm]; Defectos visuales; Aspecto OK; Masa total [g]; Resultados; Capacidad [kg/h]; Diámetro medio [mm]; Máximo [mm]; Mínimo [mm]; Delta diámetro [mm]; Mitad de delta diámetro [mm]; Tolerancia nominal [mm]

Velocidad motor | 36rpm
Velocidad puller | 1663 us
Temperatura | 200º (multímetro)
Refrigeración | Si

medir la longitud total extruida.

Toma de datos

2 | 2.82
3 | 2.93
4 | 2.23
5 | 2.73
6 | 3.51
7 | 2.06
8 | 2.81
9 | 2.18
10 | 2.60

Tolerancia sobre valor medio

2014-09-14 19:34

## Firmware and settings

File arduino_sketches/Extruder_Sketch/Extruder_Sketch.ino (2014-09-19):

/*
LCD and Encoder test code

Coding convention:

	* Variables in lowercase and underscore
	* Constants in uppercase
	* Classes starting with uppercase
	* Objects in lowercase
	* Methods and attributes in lowercase and underscore

Structure:

	* Libraries
	* Constants
	* Global variables
	* setup()
	* loop()
	* LCD and Encoder functions
	* Auxiliary functions

*/

/***************
	Libraries
****************/
#include <LiquidCrystal.h>
#include <Encoder.h>
#include <Extruder.h>

/***************
	Configuration
****************/

//Pin Constants

//LCD Pins
#define LCD_RS_PIN 48 
#define LCD_EN_PIN 49
#define LCD_D4_PIN 47
#define LCD_D5_PIN 46
#define LCD_D6_PIN 45
#define LCD_D7_PIN 44

//Screen Encoder Pins
#define S_ENC_A_PIN 20     //Encoder signal 1
#define S_ENC_B_PIN 21     //Encoder signal 2
#define S_ENC_BTN_PIN 41  //Encoder button


//Screen Constants
#define SCREEN_REFRESH_PERIOD 500	//in milliseconds. Values below 100 seems to loose encoder steps. Large values cause lag in response.
#define ENCODER_STEPS_PER_UNIT 2 	//How many steps of the encoder position are necessary to change one menu item or one variable unit
#define CURSOR_SELECT_CHARACTER 62 	//ACII code for the cursor selection character (by default 62, '>')
#define CURSOR_EDIT_CHARACTER 35 	//ACII code for the cursor edition character (by default 35, '#')

//Menu positions
#define NUMBER_OF_MENU_POSITIONS 6

#define MOTOR_MENU 0
#define HEATER_1_MENU 1
#define HEATER_2_MENU 2
#define HEATER_3_MENU 3
#define FAN_MENU 4
#define PULLER_MENU 5



/***************
	Global variables
****************/

// Instantiate the classes
LiquidCrystal lcd(LCD_RS_PIN, LCD_EN_PIN, LCD_D4_PIN, LCD_D5_PIN, LCD_D6_PIN, LCD_D7_PIN);
Encoder screen_encoder(S_ENC_A_PIN, S_ENC_B_PIN);
Extruder my_extruder;

// LCD custom chars
// Custom characters generated thanks to lcdchargen tool by Omer Kilic
// URL: http://omerk.github.io/lcdchargen/

byte motor_char[8] = {
	0b00100,
	0b00100,
	0b01110,
	0b01110,
	0b01110,
	0b01110,
	0b01110,
	0b01110
};

byte thermometer_char[8] = {
	0b00100,
	0b01010,
	0b01010,
	0b01010,
	0b01010,
	0b10001,
	0b10001,
	0b01110
};

byte fan_char[8] = {
	0b00000,
	0b11001,
	0b01011,
	0b00100,
	0b11010,
	0b10011,
	0b00000,
	0b00000
};

byte puller_char[8] = {
	0b00000,
	0b00100,
	0b01111,
	0b11111,
	0b01111,
	0b00100,
	0b00000,
	0b00000
};

byte thermometer_ON_char[8] = {
	0b00100,
	0b01010,
	0b01010,
	0b01010,
	0b01110,
	0b11111,
	0b11111,
	0b01110
};

//Screen encoder global variables
//we choose int because when the encoder lecture overflows the position increment is calculated with an error, so we want it to happen as rarely as possible
int old_screen_encoder_position = 0;
int new_screen_encoder_position;
int delta_encoder_position;
char cursor_position = 0;
char delta_cursor;
char delta_variable;


//Extruder state global variables
//declared as double to make them compatible with the PID library
//In Arduino, double has same size as float, so no increase in memory usage is compromised.
float motor_speed = 18;
double heater_1_temperature = 126;
double heater_2_temperature = 179;
double heater_3_temperature = 231;
double puller_speed = 4;
bool fan_on = 1;

//motor duty cycle
double motor_duty_cycle = 50;


//setpoints
double heater_1_setpoint = 125;
double heater_2_setpoint = 180;
double heater_3_setpoint = 225;

//heater duty cycles
double heater_1_duty_cycle = 0;
double heater_2_duty_cycle = 0;
double heater_3_duty_cycle = 0;

//Menu state variables
bool is_clicked, is_editing;

/***************
	setup()
****************/

void setup() {

	//Call the extruder setup method to manage all the initial configurartions: pin modes, operation modes, etc.
	my_extruder.setup();


	//LCD pin setup
	
	//LCD Pins
	pinMode(LCD_RS_PIN, OUTPUT);
	pinMode(LCD_EN_PIN, OUTPUT);
	pinMode(LCD_D4_PIN, OUTPUT);
	pinMode(LCD_D5_PIN, OUTPUT);
	pinMode(LCD_D6_PIN, OUTPUT);
	pinMode(LCD_D7_PIN, OUTPUT);
	
	
	//Screen Encoder Pins
	//S_ENC_A_PIN and S_ENC_B_PIN must not be initialized for the encoder to work correctly
	pinMode(S_ENC_BTN_PIN, INPUT_PULLUP); //must be connected to an internal pullup resistor
	
	// set up the LCD's number of columns and rows: 
	lcd.begin(20, 4);
	
	// setup of the custom characters
	lcd.createChar(0, motor_char);
	lcd.createChar(1, thermometer_char);
	lcd.createChar(2, fan_char);
	lcd.createChar(3, puller_char);
	lcd.createChar(4, thermometer_ON_char);

}


/***************
	loop()
****************/

void loop() {

	//First, update all the extruder subsystems

	//Update the heaters PID modules and PWM pins
	my_extruder.update_heaters();

	//Update the driver: checks whether there's cold extrusion and updates the PWM pins.
	my_extruder.update_drive();

	//Updatesthe puller output pins
	my_extruder.update_puller();

	//Update the fan output pins
	my_extruder.update_fan();


	//Second, update the LCD screen every SCREEN_REFRESH_PERIOD seconds

	static unsigned long last_screen_update; //type is return type of the millis() function


	if (millis() - last_screen_update >= SCREEN_REFRESH_PERIOD) {

		last_screen_update = millis();

		read_encoder_button();

		refresh_screen();

		read_encoder_rotation();


		// if we are in selecting mode, update the cursor
		if (is_editing == 0) {

			select_mode();

		}
		else {

			edit_mode();

		}
	}
}

/***************
	LCD and Encoder functions
****************/

void read_encoder_button(){

	//read encoder button and change menu state

	//update the button state
	if ( digitalRead(S_ENC_BTN_PIN) == HIGH ){
		is_clicked = 0;  //button is pulled up and gives a HIGH when its not pushed
	} else {
		is_clicked = 1;
	}

	//update the menu mode (selecting or editing)
	if ( is_editing == 0 && is_clicked == 1){ //if we are in selecting mode and the button is pushed, enter editing mode
	    is_editing = 1;
	} else if (is_editing == 1 && is_clicked == 1){ //if we are in editing mode and the button is pushed, leave editing mode
		is_editing = 0;
	}
}


void refresh_screen(){

	//refresh screen and draw all the characters

	//Represent the custom characters in the screen
	lcd.setCursor(1, 0);
	lcd.write((uint8_t)0); //motor_char

	lcd.setCursor(1, 1);
	if ( my_extruder.is_heater_ON(1) == 1 ){
	    lcd.write((uint8_t)4); //thermometer_ON_char
	} else {
		lcd.write((uint8_t)1); //thermometer_char
	}
	
	
	lcd.setCursor(1, 2);
	if ( my_extruder.is_heater_ON(2) == 1 ){
	    lcd.write((uint8_t)4); //thermometer_ON_char
	} else {
		lcd.write((uint8_t)1); //thermometer_char
	}
	
	lcd.setCursor(1, 3);
	if ( my_extruder.is_heater_ON(3) == 1 ){
	    lcd.write((uint8_t)4); //thermometer_ON_char
	} else {
		lcd.write((uint8_t)1); //thermometer_char
	}
	
	lcd.setCursor(10, 0);
	lcd.write((uint8_t)2); //fan_char
	
	lcd.setCursor(10, 1);
	lcd.write((uint8_t)3); //puller_char

	//Write the variable values:

	//Motor
	motor_speed = my_extruder.read_motor_speed();
	lcd.setCursor(2, 0);
	lcd.print( dto3char( (double)motor_speed) );
	
	lcd.setCursor(5, 0);
	lcd.print('/');
	
	motor_duty_cycle = 100*my_extruder.get_motor_duty_cycle();
	lcd.setCursor(6, 0);
	lcd.print( dto3char(motor_duty_cycle) );
	
	//Heater 1
	heater_1_temperature = my_extruder.read_heater_temperature(1);
	lcd.setCursor(2, 1);
	lcd.print( dto3char(heater_1_temperature) );
	
	lcd.setCursor(5, 1);
	lcd.print('/');
	
	heater_1_setpoint = my_extruder.get_heater_temperature_setpoint(1);
	lcd.setCursor(6, 1);
	lcd.print( dto3char(heater_1_setpoint) );
	
	//Heater 2
	heater_2_temperature = my_extruder.read_heater_temperature(2);
	lcd.setCursor(2, 2);
	lcd.print( dto3char(heater_2_temperature) );
	
	lcd.setCursor(5, 2);
	lcd.print('/');
	
	heater_2_setpoint = my_extruder.get_heater_temperature_setpoint(2);
	lcd.setCursor(6, 2);
	lcd.print( dto3char(heater_2_setpoint) );
	
	//Heater 3
	heater_3_temperature = my_extruder.read_heater_temperature(3);
	lcd.setCursor(2, 3);
	lcd.print( dto3char(heater_3_temperature) );
	
	lcd.setCursor(5, 3);
	lcd.print('/');
	
	heater_3_setpoint = my_extruder.get_heater_temperature_setpoint(3);
	lcd.setCursor(6, 3);
	lcd.print( dto3char(heater_3_setpoint) );
	
	//Fan
	fan_on = my_extruder.is_fan_ON();
	lcd.setCursor(11, 0);
	lcd.print(fan_on);
	
	//Puller
	puller_speed = my_extruder.get_puller_pulse_width();
	lcd.setCursor(11, 1);
	lcd.print( ito4char(puller_speed) );

}


void read_encoder_rotation(){

	//read the encoder increment in position

	//read the screen encoder position
	new_screen_encoder_position = screen_encoder.read();
	
	//calculate the increment (delta) in encoder position since last execution
	delta_encoder_position = new_screen_encoder_position - old_screen_encoder_position;
	
	//once we have finished calculating, store the last value of the screen encoder
	old_screen_encoder_position = new_screen_encoder_position;
	
	//if the screen encoder position is "about" to overflow the int range, return it to zero
	if ( (screen_encoder.read() >= 32000) || (screen_encoder.read() < -32000) ) {
		screen_encoder.write(0);
	}

}

void select_mode(){

	//Calculate the increment (delta) in the position of the cursor
	delta_cursor = delta_encoder_position / ENCODER_STEPS_PER_UNIT;

	//Clear the cursor character in the old position before the cursor is updated
	if (cursor_position <= 3){
		lcd.setCursor(0, cursor_position);
	}
	//if the menu item is in the right column
	else {
		lcd.setCursor(9, cursor_position - 4);
	}
	lcd.write(' ');

	//Calculate the new cursor position
	//If the cursor position has gone out of the range determined by NUMBER_OF_MENU_POSITIONS, return it back
	cursor_position = cursor_position + delta_cursor;
	
	while(cursor_position >= NUMBER_OF_MENU_POSITIONS ){
		cursor_position = cursor_position - NUMBER_OF_MENU_POSITIONS;
	}
	
	while(cursor_position < 0){
		cursor_position = cursor_position + NUMBER_OF_MENU_POSITIONS;
	}
	
	// Print the selection cursor
	//if the menu item is in the left column
	if (cursor_position <= 3){
		lcd.setCursor(0, cursor_position);
	}
	//if the menu item is in the right column
	else {
		lcd.setCursor(9, cursor_position - 4);
	}
	lcd.write(CURSOR_SELECT_CHARACTER);
}


void edit_mode(){
	
	//if is editing, firstly substitute the selection character by the edition character
	if (cursor_position <= 3){
		lcd.setCursor(0, cursor_position);
	}
	//if the menu item is in the right column
	else {
		lcd.setCursor(9, cursor_position - 4);
	}
	lcd.write(CURSOR_EDIT_CHARACTER);

	// update the increment (delta) of the variable to edit
	delta_variable = delta_encoder_position / ENCODER_STEPS_PER_UNIT;

	switch (cursor_position) { //depending on the menu selected, perform the editing action
	    
	    case MOTOR_MENU:

	    	motor_duty_cycle += delta_variable;
	    	my_extruder.set_motor_duty_cycle(motor_duty_cycle/100);
	    	break;

	    case HEATER_1_MENU:

	    	heater_1_setpoint += delta_variable;
	    	my_extruder.set_heater_temperature_setpoint(1, heater_1_setpoint);
	    	break;

	    case HEATER_2_MENU:

	    	heater_2_setpoint += delta_variable;
	    	my_extruder.set_heater_temperature_setpoint(2, heater_2_setpoint);
	    	break;

	    case HEATER_3_MENU:

	    	heater_3_setpoint += delta_variable;
	    	my_extruder.set_heater_temperature_setpoint(3, heater_3_setpoint);
	    	break;

	    case FAN_MENU:
	    	
	    	//if the encoder has been turned and odd number of times, change the state of the fan
	    	//(and even number of state changes would lead to the same initial state)
	    	if ( (delta_variable != 0) && (delta_variable%2 == 1) ){
	    		if (my_extruder.is_fan_ON() == 1){
	    			//if the fan is ON, turn it OFF
	    			my_extruder.set_fan_OFF();
	    		}
	    		else{
	    			//if the fan is OFF, turn it ON
	    			my_extruder.set_fan_ON();
	    		}
	    	}
	    	break;

	    case PULLER_MENU:
	    	puller_speed += delta_variable;
	    	my_extruder.set_puller_pulse_width(puller_speed);
	    	break;
	}
}

/***************
	Auxiliary functions
****************/

//auxiliary functions used to convert variables to character arrays that can be represented in the LCD screen

char conv[5];

char * dto3char(double d){
	//takes the double d and returns the string in format "123" (no decimals, three digits)
	int i = (int)d;
	
	//error
	if (d > 999 || d < 0){
		conv[0] = 'E';
		conv[1] = 'R';
		conv[2] = (d>=0)?'+':'-';
		conv[3] = 0;
	}
	else {
		//hundreds
		if (d >= 100.0){
			conv[0] = (i/100) + '0';
		}
		else {
			conv[0] = ' ';
		}
		//tens
		if (d >= 10.0){
			conv[1] = (i%100)/10 + '0';
		}
		else {
			conv[1] = ' ';
		}
		//units
		conv[2] = (i%10) + '0';
		
		//end of string
		conv[3] = 0;
	}

	return conv;
}

char * ito4char(int i){
	
	//errors
	if (i > 9999 || i < 0){
		conv[0] = 'E';
		conv[1] = 'R';
		conv[2] = (i>=0)?'+':'-';
		conv[3] = 0;
	}
	else {
		if (i >= 1000){
			conv[0] = (i/1000) + '0';
		}
		else {
			conv[0] = ' ';
		}
		//hundreds
		if (i >= 100){
			conv[1] = (i%1000)/100 + '0';
		}
		else {
			conv[1] = ' ';
		}
		//tens
		if (i >= 10){
			conv[2] = (i%100)/10 + '0';
		}
		else {
			conv[2] = ' ';
		}
		//units
		conv[3] = (i%10) + '0';
		
		//end of string
		conv[4] = 0;
	}

	return conv;
}

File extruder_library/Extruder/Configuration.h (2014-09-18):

#ifndef Configuration_h_
#define Configuration_h_

/***************************
 *	Configuration.h
 *
 *	This file constains all the default and initial values
 *	necessary for the configuarion of the extruder.
 *
****************************/


/***************************
 *	Pins
****************************/

#define MOTOR_PWM_PIN 4 	//Pin that outputs the PWM control signal (white)
#define MOTOR_LOW_PIN 5 	//Pin that allways is LOW (grey)

#define MOTOR_ENCODER_1_PIN 3 	//white cable
#define MOTOR_ENCODER_2_PIN 2 	//brown cable

//PWM pins for the heaters
#define HEATER_1_PWM_PIN 11
#define HEATER_2_PWM_PIN 10
#define HEATER_3_PWM_PIN 9
#define HEATER_4_PWM_PIN 12345
#define HEATER_5_PWM_PIN 12345


//Put PWM pins in an array for the constructor to have easy sequential access to them
//Index correspond to heater number (from 1 to 5; 0 is empty)
const char HEATER_PWM_PIN[6] = {0, HEATER_1_PWM_PIN, HEATER_2_PWM_PIN, HEATER_3_PWM_PIN, HEATER_4_PWM_PIN, HEATER_5_PWM_PIN};

//Analog pins for the thermistors
#define HEATER_1_THERMISTOR_PIN 2
#define HEATER_2_THERMISTOR_PIN 1
#define HEATER_3_THERMISTOR_PIN 0
#define HEATER_4_THERMISTOR_PIN 12345
#define HEATER_5_THERMISTOR_PIN 12345

//Put all thermistor pins in an array for the constructor to have easy sequential access to them
//Index correspond to heater number (from 1 to 5; 0 is empty)
const char HEATER_THERMISTOR_PIN[6] = {0, HEATER_1_THERMISTOR_PIN, HEATER_2_THERMISTOR_PIN, HEATER_3_THERMISTOR_PIN, HEATER_4_THERMISTOR_PIN, HEATER_5_THERMISTOR_PIN};


#define PULLER_PIN 12

#define FAN_PIN 8


/***************************
 *	Drive configuration
****************************/

#define MOTOR_ENCODER_STEPS_PER_REVOLUTION 1200


/***************************
 *	Heater configuration
****************************/

#define NUMBER_OF_HEATERS 3	//library supports by default up to 5 heaters

//Constants used to prevent cold extrusion
#define MELTING_HEATERS 1 				//Number of heaters, starting from (and including) heater 1, in which plastic is in molten state.
#define MELTING_TEMPERATURE 150 		//If the melting heaters are below this temperature, the motor can't be turned on (0 to deactivate feature)

//Heater PWM limit (used to limit the power of the heaters)
#define HEATER_MAX_PWM 0.8 //value from 0 to 1

//Maximum and minimun heater temperatures
#define HEATER_MAX_TEMPERATURE 300 	//Celsius
#define HEATER_MIN_TEMPERATURE 0 	//Celsius

//Heater initial temperature setpoints
//Numbering criteria: heater 1 is the one nearest the die, heater 5 is the farthest.
#define HEATER_1_SETPOINT 60
#define HEATER_2_SETPOINT 60
#define HEATER_3_SETPOINT 60
#define HEATER_4_SETPOINT 0 
#define HEATER_5_SETPOINT 0

//Put all the setpoints in an array for the constructor to have easy sequential access to them
//Index correspond to heater number (from 1 to 5; 0 is empty)
const double HEATER_SETPOINT[6] = {0, HEATER_1_SETPOINT, HEATER_2_SETPOINT, HEATER_3_SETPOINT, HEATER_4_SETPOINT, HEATER_5_SETPOINT};

//Heater default PID parameters

#define HEATER_1_K_P 2.0
#define HEATER_1_K_I 5.0
#define HEATER_1_K_D 0

#define HEATER_2_K_P 2.0
#define HEATER_2_K_I 5.0
#define HEATER_2_K_D 0

#define HEATER_3_K_P 2.0
#define HEATER_3_K_I 5.0
#define HEATER_3_K_D 0

#define HEATER_4_K_P 2.0
#define HEATER_4_K_I 5.0
#define HEATER_4_K_D 0

#define HEATER_5_K_P 2.0
#define HEATER_5_K_I 5.0
#define HEATER_5_K_D 0

//Put all PID constants in an array for the constructor to have easy sequential access to them
//Index correspond to heater number (from 1 to 5; 0 is empty)
const double HEATER_K_P[6] = {0, HEATER_1_K_P, HEATER_2_K_P, HEATER_3_K_P, HEATER_4_K_P, HEATER_5_K_P};
const double HEATER_K_I[6] = {0, HEATER_1_K_I, HEATER_2_K_I, HEATER_3_K_I, HEATER_4_K_I, HEATER_5_K_I};
const double HEATER_K_D[6] = {0, HEATER_1_K_D, HEATER_2_K_D, HEATER_3_K_D, HEATER_4_K_D, HEATER_5_K_D};
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

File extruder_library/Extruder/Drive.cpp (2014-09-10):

#include "Drive.h"

#include "Arduino.h"

	//Constructors:

	//Empty constructor
	Drive::Drive(){
		//not implemented, use parametrized constructor
	}
	//Parametrized constructor
	Drive::Drive(char motor_pwm_pin, char motor_low_pin, char encoder_1_pin, char encoder_2_pin,  int encoder_steps_per_revolution){
		//Pins
		_motor_pwm_pin = motor_pwm_pin;
		_motor_low_pin = motor_low_pin;
		_encoder_1_pin = encoder_1_pin;
		_encoder_2_pin = encoder_2_pin;

		//Initialize the duty cycle at 0 (motor stopped) to avoid cold extrusion
		_motor_duty_cycle = 0.0;

		_encoder = new Encoder(encoder_1_pin, encoder_2_pin);
		
		_encoder_steps_per_revolution = encoder_steps_per_revolution;

		_last_micros = 0 ;
	}


	//Destructor:

	Drive::~Drive(){
		delete _encoder;
	}

	//Methods:

	//Configuration. Code that has to be runned at setup()
	void Drive::setup(){
		pinMode(_motor_pwm_pin, OUTPUT); 	//IN2 pin, controls the red terminal of the motor (V+, PWM Speed control
		pinMode(_motor_low_pin, OUTPUT); 	//IN1 pin, controls the black terminal of the motor (GND)
	}

	//Update drive output pins
	void Drive::update(){
		analogWrite(_motor_pwm_pin, _motor_duty_cycle*255.0);
		digitalWrite(_motor_low_pin, LOW);
	}

	//Checks if the motor is running (that is, _motor_duty_cycle > 0)
	bool Drive::is_ON(){
		if (_motor_duty_cycle > 0.0){
			return 1;
		}
		else {
			return 0;
		}
	}

	//Read the motor speed using the encoder
	double Drive::read_motor_speed(){

		double motor_speed, motor_position;
		
		//read the encoder position
		motor_position = _encoder->read();
		
		//calculate speed
		motor_speed = (motor_position/ _encoder_steps_per_revolution )/(micros()-_last_micros);
		  
		//convert from rev/us to rev/min
		motor_speed = motor_speed*600000;
		  
		//store the last_micros value and clear the encoder position
		_last_micros = micros();
		_encoder->write(0);
		  
		return motor_speed;
	}

	//Get the motor duty cycle
	double Drive::get_motor_duty_cycle(){
		return _motor_duty_cycle;
	}

	//Set the motor dudy cycle
	void Drive::set_motor_duty_cycle(double motor_duty_cycle){
		//Duty cycles above 1 or below 0 are not allowed
		if (motor_duty_cycle >= 1.0) {
			_motor_duty_cycle = 1.0;
		}
		else if (motor_duty_cycle <= 0){
			_motor_duty_cycle = 0;
		}
		//If the temperature is in the acceptable range
		else {
			_motor_duty_cycle = motor_duty_cycle;
		}	
	}

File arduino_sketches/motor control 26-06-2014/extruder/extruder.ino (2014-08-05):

#include <Encoder.h>
#include <LiquidCrystal.h>

// LCD Keyboard buttons
#define btnRIGHT  0
#define btnUP     1
#define btnDOWN   2
#define btnLEFT   3
#define btnSELECT 4
#define btnNONE   5

// Display screens
#define screenScrewSpeed    0
#define screenTemperature1  1
#define screenTemperature2  2

//RGB LED Pins
#define redRGBLEDPin 13
#define greenRGBLEDPin 12
#define blueRGBLEDPin 11

// LCD panel pins

#define LCD_RS_PIN 8 
#define LCD_EN_PIN 9
#define LCD_D4_PIN 4
#define LCD_D5_PIN 5
#define LCD_D6_PIN 6
#define LCD_D7_PIN 7

LiquidCrystal lcd(LCD_RS_PIN, LCD_EN_PIN, LCD_D4_PIN, LCD_D5_PIN, LCD_D6_PIN, LCD_D7_PIN);

//LiquidCrystal lcd(8, 9, 4, 5, 6, 7);

int lcd_screen = 0; //selected screen
int previous_lcd_screen = 1; //last screen, used to update the setpoint values

int lcd_key = 0; //pressed key
int previous_lcd_key = 1; //last pressed key, used to detect state changes


// Extruder variables
float screwSpeed = 1;
float temperature1 = 2;
float temperature2 = 3;

// Setpoint values
float screwSpeedSetpoint = 0;
float temperature1Setpoint = 0;
float temperature2Setpoint = 0;

// Current extruder variable and setpoint
float currentValue = 0;
float currentSetpoint = 0;

float previousValue = 0;
float previousSetpoint = 0;


//Read the pressed button from the LCD keypad
int read_LCD_buttons() {
  /*******************************************************
  This function has been written from the code by Mark Bramwell, July 2010
  Found in: http://www.dfrobot.com/wiki/index.php?title=Arduino_LCD_KeyPad_Shield_%28SKU:_DFR0009%29
  ********************************************************/

  int adc_key_in;
  adc_key_in = analogRead(0); //read value of the keypad analog output
  
  // my buttons when read are centered at these valies: 0, 144, 329, 504, 741
  // we add approx 50 to those values and check to see if we are close
  if (adc_key_in > 821)  return btnNONE; // We make this the 1st option for speed reasons since it will be the most likely result
  if (adc_key_in < 50)   return btnRIGHT; 
  if (adc_key_in < 176)  return btnUP;
  if (adc_key_in < 328)  return btnDOWN;
  if (adc_key_in < 518)  return btnLEFT;
  if (adc_key_in < 821)  return btnSELECT;

  return btnNONE;
}

// Emergency bit, set to 1 if something doesn't work
char emergency = 1;

void setRGBLED(){
  if (emergency == 1){
    digitalWrite(redRGBLEDPin, HIGH);
    digitalWrite(blueRGBLEDPin, LOW);
    digitalWrite(greenRGBLEDPin, LOW);
  }
  else {
    digitalWrite(redRGBLEDPin, LOW);
    digitalWrite(blueRGBLEDPin, LOW);
    digitalWrite(greenRGBLEDPin, HIGH);
  }
}

void setEmergencyLED(){
  if(emergency == 1){
    digitalWrite(13, HIGH);
  }
  else {
    digitalWrite(13, LOW);
  }
}

Encoder MotorEncoder(2, 3); //Brown cable in pin 3
                            //White cable in pin 2
                            
unsigned long last_micros = 0;

float getScrewSpeed(){
  
  float motor_speed, motor_position;
  
  motor_position = MotorEncoder.read();
  
  motor_speed = (motor_position/1200.0)/(micros()-last_micros);
  
  //convert from rev/us to rev/min
  motor_speed = motor_speed*600000;
  
  //store the last_micros value
  last_micros = micros();
  MotorEncoder.write(0); 
  
  return motor_speed;
}

float pot_read = 0;
float motor_duty_cycle = 0;


void setup(){
  lcd.begin(16, 2);              // start the library
  
  pinMode(11, OUTPUT); //IN2 pin, controls the red terminal of the motor (V+, PWM Speed control
  pinMode(12, OUTPUT); //IN1 pin, controls the black terminal of the motor (GND)
  pinMode(0, INPUT); //SF flag
  
  pinMode(13, OUTPUT); //emergency LED pin
}

void loop(){
  
  screwSpeed = getScrewSpeed();
  
  pot_read = analogRead(1);
  motor_duty_cycle = pot_read/1023.0; 

  lcd.setCursor(0,0);
  lcd.print("Motor Speed     ");
  lcd.setCursor(0,1);
  lcd.print(screwSpeed);
  lcd.setCursor(9,1);
  lcd.print(motor_duty_cycle);
 
  if (digitalRead(0) == LOW){ //check SF flag for overtemperature or shorts (active if LOW)
    emergency = 1;
  } else {
    emergency = 0;
  }
  
  
  
  
  digitalWrite(12, LOW);
  analogWrite(11, motor_duty_cycle*255.0);
  
  setEmergencyLED();
  
  
}

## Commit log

2014-07-10 Uploaded all initial files
    [fan_duct.fcstd, fan_support.fcstd, motor_support.FCStd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]
2014-07-10 Motor weight supports adapted to 50mm height
    [vslot_motor_support_big.fcstd, vslot_motor_support_big.stl, vslot_motor_support_small.fcstd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]
2014-07-10 Named all operations, holes adapted to slot
    [motor_torsion_support.fcstd, motor_torsion_support.stl]
2014-07-13 Renamed all operations
    [thrust_bearing_support.fcstd]
2014-07-13 Uploaded new files
    [filament_line_assembly.fcstd, motor_simplified.fcstd, pipe_support.FCStd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]
2014-07-16 Design and upload of shaft coupler files
    [shaft_coupler_blank.fcstd, shaft_coupler_hex.fcstd, shaft_coupler_hex.stl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]
2014-07-16 Work on pipe_support
    [pipe_suport.stl, pipe_support.FCStd]
2014-07-16 Work on Line Assembly
    [filament_line_assembly.fcstd]
2014-07-22 First version of the new pipe support and hopper prototype
    [pipe_and_hopper_strong.fcstd, pipe_and_hopper_strong.stl]
2014-07-22 Modified pipe_support
    [pipe_support.FCStd]
2014-07-26 Smaller hole
    [shaft_coupler_hex.fcstd, shaft_coupler_hex.stl]
2014-07-29 First version of the pipe and hopper support
    [pipe_and_hopper.fcstd, pipe_and_hopper.stl]
2014-07-31 First version of the thrust_bearing_support
    [thrust_bearing_support.fcstd, thrust_bearing_support.stl]
2014-08-01 First version of the unibody hopper extension
    [hopper.fcstd, hopper.stl]
2014-08-01 Smaller hopper bottom to accommodate screw heads
    [hopper.stl]
2014-08-01 Smaller hopper bottom
    [hopper.fcstd]
2014-08-01 Smaller hopper to accommodate screw heads
    [hopper.fcstd, hopper.stl]
2014-08-01 Unibody motor support first version
    [motor_support.fcstd, motor_support.stl]
2014-08-02 New save
    [motor_support.fcstd]
2014-08-02 New file
    [motor_support.fcstd]
2014-08-23 Last week development
    [fan_holder_left.fcstd, fan_holder_left.stl, fan_holder_right.fcstd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]
2014-09-01 New Unibody iteration 2
    [hopper.fcstd, hopper.stl, hopper_and_barrel_support.fcstd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]
2014-09-01 Initial upload of LCD holder
    [lcd_holder.fcstd, lcd_holder.stl]
2014-09-01 Initial version of the sketch with the Extruder library
2014-09-01 Drive organized in multiple directories
    [motor_simplified.fcstd, motor_support.FCStd, motor_support_small.stl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]
2014-09-01 Fixed vslot holes
    [lcd_holder.fcstd, lcd_holder.stl]
2014-09-01 Prototype corrections
    More rigid LCD stand
    Higher LCD stand
    No vslot chamfer
    [lcd_holder.fcstd, lcd_holder.stl]
2014-09-05 Uploaded heater schematics
    [heater_module_electronics.sch]
2014-09-05 Changed some names
    [heater_module_electronics.sch]
2014-09-05 Added the flyback diode to schematic
    [heater_module_electronics.sch]
2014-09-05 Initial library upload
    [Configuration.h]
2014-09-06 Added fan control electronics schematics
    [fan_control_electronics.sch]
2014-09-06 Created exploded model of the unibody printed parts
    [unibody_drive_exploded.fcstd]
2014-09-09 Added the cooling fan support
2014-09-09 Many unibody improvements and uploads
    - Organized in new subdirectories structure
    - New assembled and exploded assembly models
    - Many new drawings
    [M3-hex-nut.fcstd, M3x10-cylinder-hex-head.fcstd, M3x40-cylinder-hex-head.fcstd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]
2014-09-10 Uploaded Auger model
    [Bosch_625_Auger.STL]
2014-09-10 Relocated motor
    [motor_simplified.fcstd]
2014-09-10 Updated motor torsion support
    [motor_torsion_support.fcstd]
2014-09-10 New extruder assembly
    [unibody_drive_assembled.fcstd]
2014-09-10 Fan support and removed motor SF pin
    [Configuration.h]
2014-09-11 Changed name from auger to screw
    [Bosch_625_Auger.STL]
2014-09-11 Made a simplified model of the screw
    Reason is complete model is too heavy on my computer
    [screw_simplified.fcstd]
2014-09-11 Updates on the assembled drive
    [unibody_drive_assembled.fcstd]
2014-09-11 Added bearing models
    [flanged_bearing.fcstd, plain_bearing.FCStd, thrust_bearing.fcstd]
2014-09-11 Added mechanical subsystem assembly
    [mechanical_assembly.fcstd]
2014-09-15 Barrel files
    [4452K114.STEP, 4452K144.STEP, 44695K110.STEP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]
2014-09-15 First prototype assembly
    [prototype_assembly.fcstd]
2014-09-15 Moved motor_torsion_support to the correct folder
    [motor_torsion_support.fcstd]
2014-09-15 Work on the extruder assembly
    Added barrel and screw
2014-09-18 Clean and comment the Extruder library
    [Configuration.h]
2014-10-04 Bachelor thesis material
